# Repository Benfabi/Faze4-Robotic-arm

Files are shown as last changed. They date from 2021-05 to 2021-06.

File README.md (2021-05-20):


# Faze4-Robotic-arm

 

Faze4 is small fully 3d printable Open source 6 axis robotic arm. It is functionally and esthetically similar to robotic arms in industry but is aimed for research, education and  anyone interested in making his own robot arm. 

The whole arm has around 1000 parts (including screws and bearings) and weights around 15 kg.

## Why this fork?

The original repository contains many links, PDFs and most likely everyhting you need to create the Faze4 robot. However, it does not really give a sense of a structured approach building it, writing software for the robot or using it in the end.

At this point, this fork is supposed to contribute. It should give a clear direction where to start and how to build it, independent of your background.

# Structure of this repo

- [0-Construction](./0-Construction): this folder contains a step by tutorial building the robot.
- [STL](./STL): this folder contains the STL files to print. The construction tutorial will let you know when each print is needed. 
- [Original](./Original): this folder contains the files from the original repository.

# Where to start ? 

It is recommended to start with the [Construction](./0-Construction) folder.

# Check the arm in action
Check the arm in action ! (https://www.youtube.com/watch?v=OHw6_l_8Tnk)

# Further Links:

- [Building instructions](./Original/Assembly%20instructions%203.1.pdf)
- [DOCS](https://faze4-robotic-arm-docs.readthedocs.io/en/latest/) Contains ALL info about the arm.
- [URDF files](https://github.com/PCrnjak/Faze4-Robotic-arm/tree/master/URDF_FAZE4)
- [Hackaday](https://hackaday.io/project/167247-faze4-robotic-arm)
- [DOCS](https://faze4-robotic-arm-docs.readthedocs.io/en/latest/)

# Project is under MIT Licence

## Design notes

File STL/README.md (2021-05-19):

# STL files

This folder contains the STL files that are needed to build the robot. 
I also put the GCode files here that I used to print the specific parts.

The printer I use is a [Original Prusa i3 MK3S+ Drucker
](https://shop.prusa3d.com/3d-drucker/181-original-prusa-i3-mk3s-drucker.html).

The slicer settings used are in the corresponding 3mf file.

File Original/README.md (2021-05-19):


# Faze4-Robotic-arm

 

Faze4 is small fully 3d printable Open source 6 axis robotic arm. It is functionally and esthetically similar to robotic arms in industry but is aimed for research, education and 
anyone interested in making his own robot arm. 
Main "selling points" of this arm that separate it from other DIY arms are:

* It is cheap <1000 dollars.
* Uses 3d printed cycloidal gearboxes which have low backlash and can be repaired really easy.
* All wires are hidden giving it really clean design.

Whole arm has around 1000 parts (including screws and bearings) and weights around 15 kg.

# Check the arm in action !
Check the arm in action ! (https://www.youtube.com/watch?v=OHw6_l_8Tnk)

# Where to start ? 

To build this robotic arm follow [Building instructions](https://github.com/PCrnjak/Faze4-Robotic-arm/blob/master/Assembly%20instructions%203.0.pdf). All general info about robotic arm is in [DOCS](https://faze4-robotic-arm-docs.readthedocs.io/en/latest/). Building instructions and DOCS go hand in hand and you need to follow both to build this arm. Building instructions are about general mechanical assembly while DOCS contain ALL info ( Electrical wiring, Low level setup, High level ROS and Matlab, tips ...).

# Contents:

- [Low level code]() coming soon
- [High level code (ROS and Matlab)]() coming soon
- [Building instructions](https://github.com/PCrnjak/Faze4-Robotic-arm/blob/master/Assembly%20instructions%203.0.pdf)
- [BOM](https://github.com/PCrnjak/Faze4-Robotic-arm/blob/master/Bom_1.2_joint2_update.xlsx) 
- [DOCS](https://faze4-robotic-arm-docs.readthedocs.io/en/latest/) Contains ALL info about the arm.
- [URDF files](https://github.com/PCrnjak/Faze4-Robotic-arm/tree/master/URDF_FAZE4) 

# Where to see more Faze4 robotic arm?
- [Youtube](https://www.youtube.com/channel/UCp3sDRwVkbm7b2M-2qwf5aQ)
- [Hackaday](https://hackaday.io/project/167247-faze4-robotic-arm)
- [DOCS](https://faze4-robotic-arm-docs.readthedocs.io/en/latest/)

# Support the project

This project is completely Open source and free to all and I would like to keep it that way, so any help 
in terms of donations or advice is really appreciated. Thank you!

Check the arm in action ! (https://paypal.me/PCrnjak?locale.x=en_US)

# Project is under MIT Licence

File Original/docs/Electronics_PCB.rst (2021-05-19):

Electronics, PCB and wiring
===========================

.. meta::
   :description lang=en: info about Electronics and PCB.
   
All electronics can also be bought from ebay and similar sites. I used cheap stepper drivers from ebay but you can buy any stepper driver that can supply enough current for the steppers.

Check how i wired my arm in this file: FAZE4 Robotic arm electronics setup.pdf on github page:
https://github.com/PCrnjak/Faze4-Robotic-arm

.. Tip::

   From experience i found out that cheaper stepper drivers tend to make more noise, so if you want quiet robot arm buy more expensive drivers. I found ones from stepperonline good.

PCB V1
------------
This PCB is first version and has some errors that will be fixed in revision 2.
Board was created in Altium Circuitmaker and all files can be found here:

.. Warning::

  I recommend waiting for next version since this one has alot of errors.

* `All files for PCB`_

.. _All files for PCB: https://github.com/PCrnjak/Faze4-Robotic-arm/blob/master/Distribution_PCB.zip

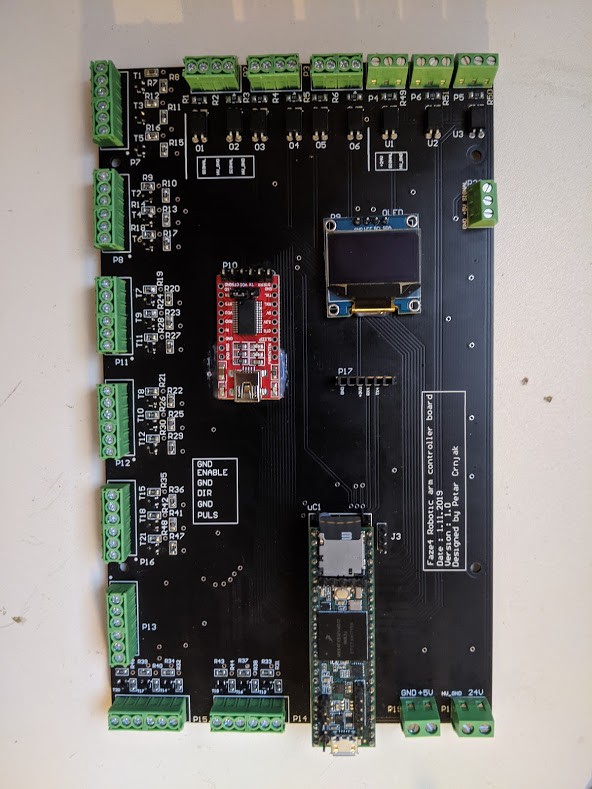
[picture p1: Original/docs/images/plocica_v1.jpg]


Upper section of PCB are Inputs for limit switches and inductive sensors. All inputs on top are isolated with optocouplers. I did that since all wires of the arm are going thru same spot, that means "high voltage" stepper wires were near low voltage limit switch wires. That caused problems where steppers induced enough voltage on limit switch wires to trigger interrupts on teensy. That is why limit switches and sensors are connected to 24v.

left side is for stepper outputs. There are also 2 stepper outputs on bottom right side.

Bottom right side has 5V input and 24V input. You need both for arm to work. In the middle we have few extra serial ports and OLED display.

When wiring stepper drivers to the PCB i used TB6600  driver pinout as reference.I planned for all drivers to be connected like picture below. HIGH signal on ENABLE + pin would enable stepper drivers. Now i made some mistakes and not all drivers can be connected like that.

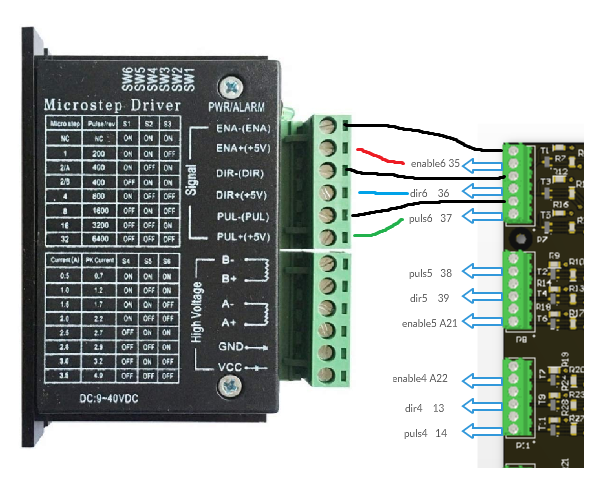
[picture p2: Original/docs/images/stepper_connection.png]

    
Now i made some mistakes and not all drivers can be connected like that. In picture below you can see how to connect all drivers. As you can see for joint 5 (connector below top one) i switched enable and puls pins. That means that puls5 pin ( pin 38 on teensy) is connected to puls pin on stepper driver. I also skipped Port that has no 5V level shifter since it didnt work well.

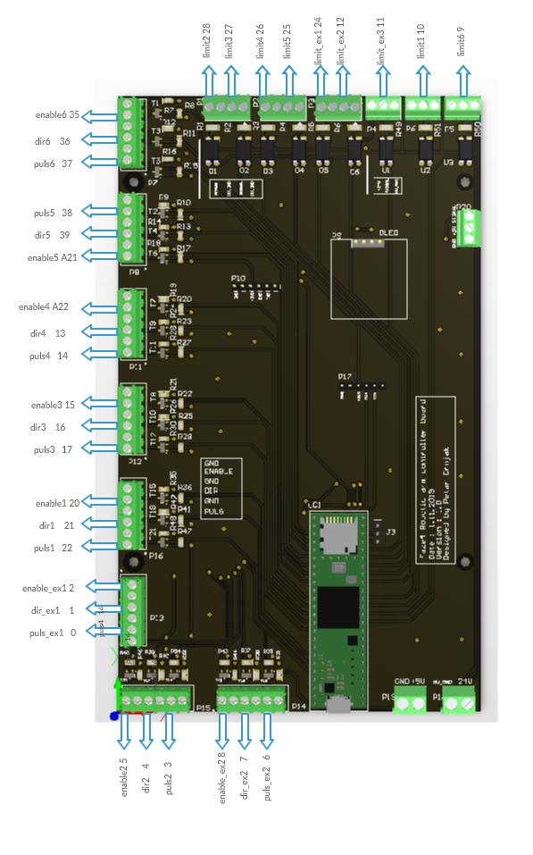
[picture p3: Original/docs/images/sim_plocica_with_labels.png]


After wiring all dir,puls and enable pins you are left with power pins on stepper driver and A- A+ B- B+ Pins. Those are quite straightforward. 
Pins that have ext in name are extra pins that are now used in my version of arm.

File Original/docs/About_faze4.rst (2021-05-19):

About Faze4
===========================

.. meta::
   :description lang=en: General info about Faze4 robotic arm.

General info
------------

Faze4 robotic arm came to be when i made a working 3d printable cycloidal gearbox and saw some potential in it. After that i designed whole arm around it. It uses 6 stepper motors, so it is a 6 axis robot arm. While designing this arm i focused on low backlash and good design of arm. All wires are hidden and arm is really rigid even tho it is 3d printed. Total cost of the arm is around 1000 - 1500 dollars.

.. note::

    This project is still work in progress. Part that is work in progress is control cabinet, that means that the arm can be built and it     will work without the cabinet.
    
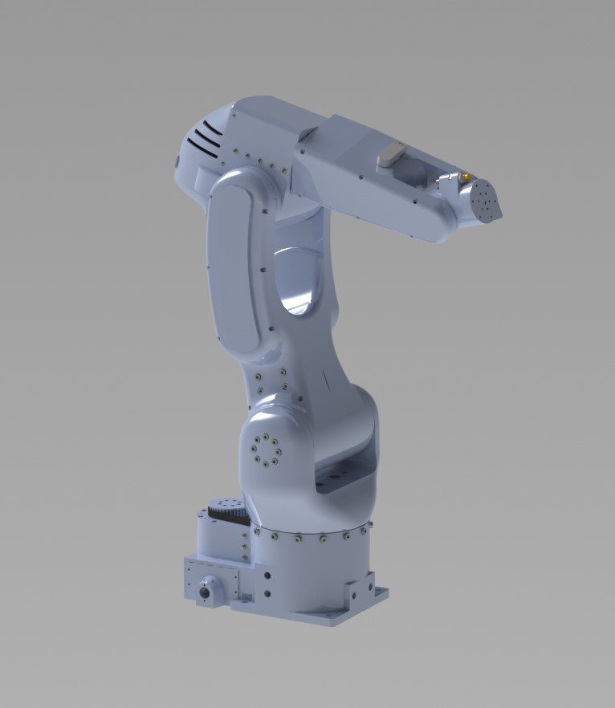
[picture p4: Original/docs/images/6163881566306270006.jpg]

    
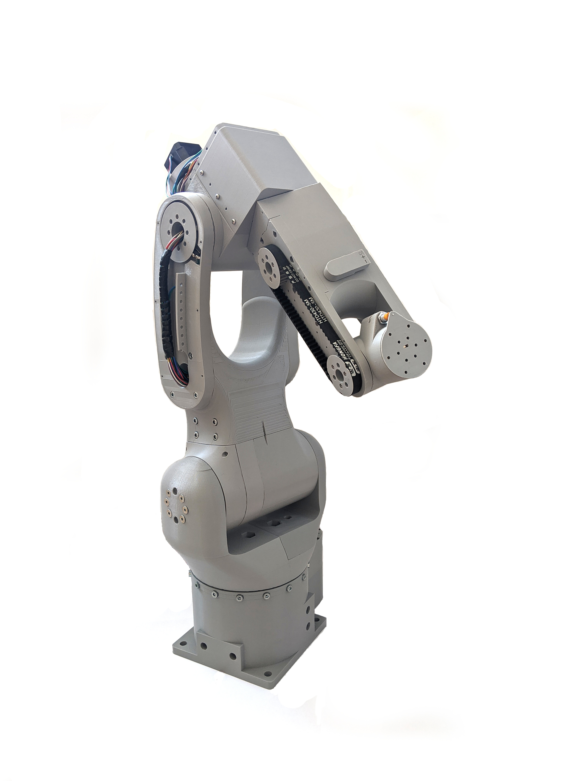
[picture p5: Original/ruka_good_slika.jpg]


Esthetic design was inspired by FANUC’s LR Mate 200iD. 
Goal was also to hide all wires in the arm like most industrial arms do. 
Only visible wires (or pipes) would be ones for gripper. 

Weight of the arm is around 14-15 kg , but it can be reduced by printing with less infill.

Low level control for the arm runs on teesny 3.5, while high level (inverse kinematics, simulations) are only on Matlab code atm, but I am working on ROS implementation and porting my Matlab code to Python.

Table of contents
-----------------

On this read the docs page you will find:

* How is arm desinged and desing decisions
* Printing tips
* Electronics guide and PCB
* Building instructions for the arm
* All code and programs used
* How to test and troubleshoot
* Sources 
* Where to buy parts

Check the arm in action !
-------------------------

.. raw:: html

    <div style="text-align: center; margin-bottom: 2em;">
    <iframe width="100%" height="350" src="https://www.youtube.com/embed/-qTVx23o6C0?rel=0" frameborder="0" allow="autoplay; encrypted-media" allowfullscreen></iframe>
    </div>

Support the project
-------------------

This project is completely Open source and free to all and I would like to keep it that way, so any help 
in terms of donations or advice is really appreciated. Thank you!

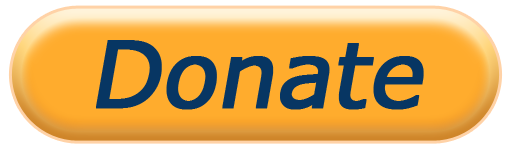
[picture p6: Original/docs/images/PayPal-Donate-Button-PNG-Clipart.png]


Thanks to the:
--------------
* `Peter Corke for his amazing robotics toolbox for Matlab`_
* `Maximilian_Schommer for his cycloidal drive generator`_

.. _Peter Corke for his amazing robotics toolbox for Matlab: https://petercorke.com/toolboxes/robotics-toolbox/
.. _Maximilian_Schommer for his cycloidal drive generator: https://forum.onshape.com/discussion/7567/cycloidal-gear-generator

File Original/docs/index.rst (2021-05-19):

.. Read the Docs documentation master file, made by Petar Crnjak.

Faze4 Robotic arm documentation
==================================================

Contents:

.. toctree::
   :maxdepth: 2
   :glob:

   *

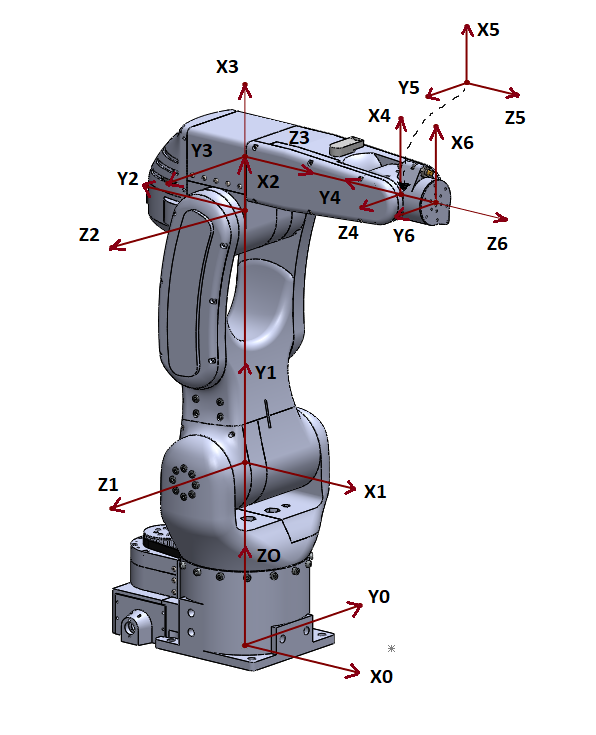
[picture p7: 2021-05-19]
Original/docs/images/OSI_v2.png

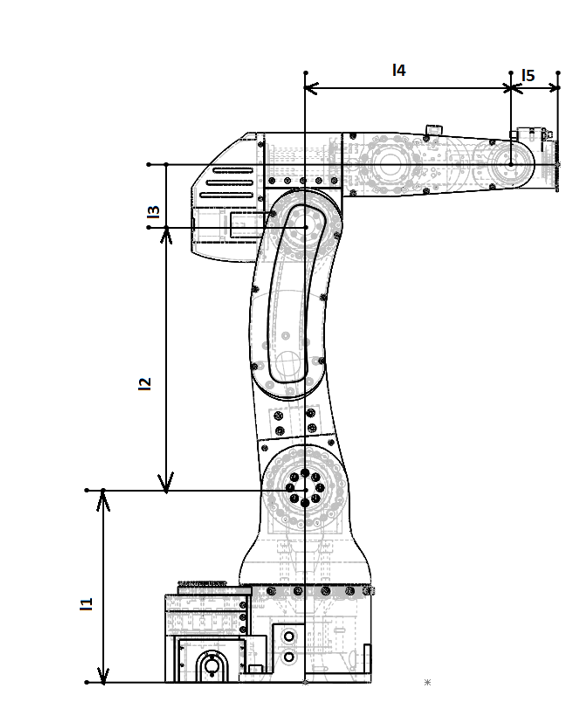
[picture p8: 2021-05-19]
Original/docs/images/robot_dim.png

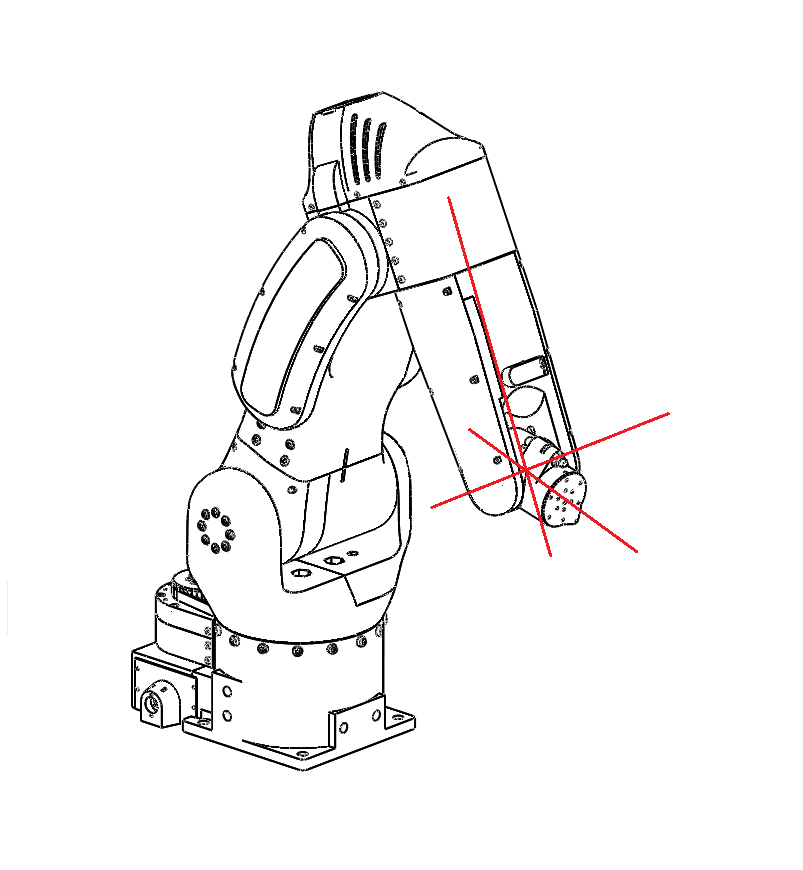
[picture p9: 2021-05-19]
Original/docs/images/slikaosirotacije.png

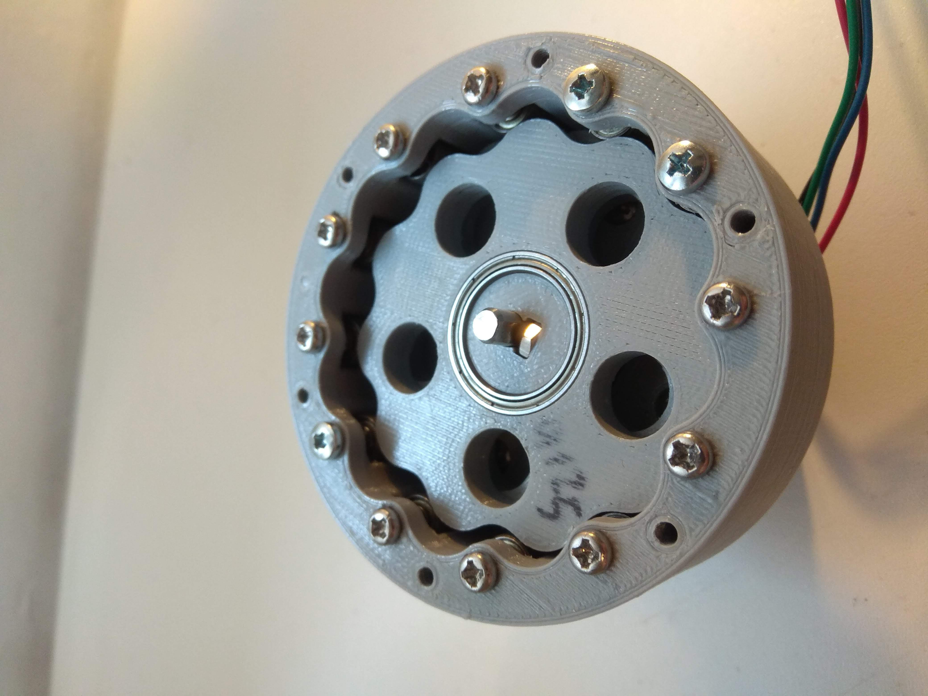
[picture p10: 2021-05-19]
Original/docs/images/reducer.jpg

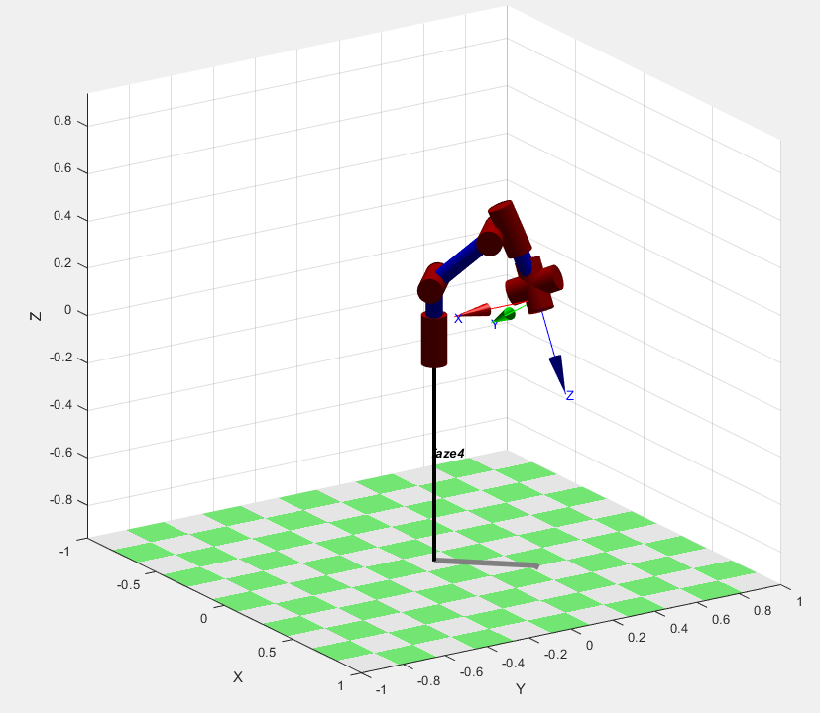
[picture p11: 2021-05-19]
Original/docs/images/30&180&90.png

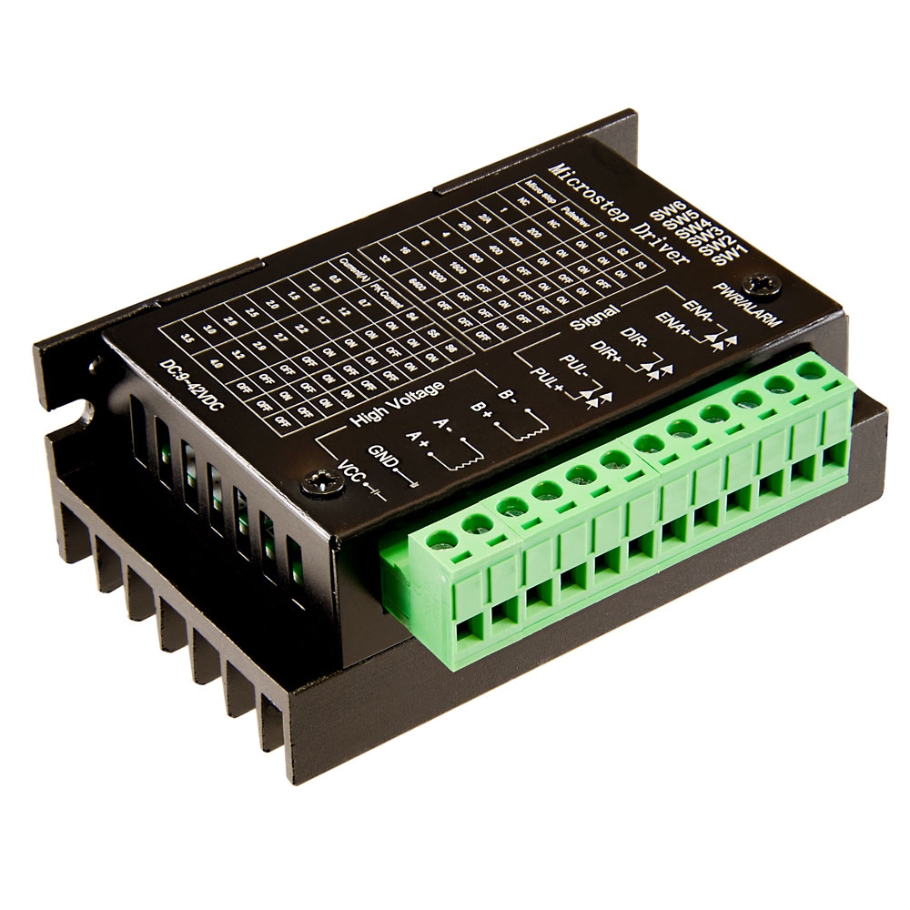
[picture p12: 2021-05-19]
Original/docs/images/tb6600.jpg

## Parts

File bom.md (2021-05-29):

# Bill of Materials

## Screws

| Diameter, length | Type | Quantity |
| ---- | --- | --- |
| M2 5mm screw | philips pan head | 3 |
| M2 8 mm screw | philips pan head | 8 |
| M2 10-12 mm screw | philips pan head | 7 |
| M3 4mm set screw | Hex | 6 |
| M3 5mm screws | philips pan head | 12 |
| M3 10 mm screw | philips pan head | 54 |
| M3 15mm screw | philips pan head | 54 |
| M3 20mm screw | philips pan head | 53 |
| M3 25mm screws | philips pan head | 64 |
| M3 30 mm screw | philips pan head | 52 |
| M5 8 mm screw | Hex socket cap | 12 |
| M5 20 mm screw | Hex socket cap | 27 |
| M5 25 mm screw | Hex socket cap | 8 |
| M5 30 mm screw | Hex socket cap | 13 |
| M5 40 mm screw | Hex socket cap | 10 |
| M10 60 mm screw | Hex socket cap | 4 |

## Nuts

| Type | Quantity |
| --- | --- |
| M2 nuts | 2 |
| M3 nuts | 6 |
| M5 nuts |	15 |
| M8 nuts (included with sensor, see other stuff) | 4 |
| M10 nuts | 4 |
| M12 nuts | 4 |

## Ball Bearings

| Ball Bearing Type | Quantity |
| --- | --- |
|  35x47x7  | 8 |
|  3x8x4 | 200 |
|  17x23x4  | 4 |
|  15x28x7  | 6 |
|  3x10x4 | 40 |
|  50x67x7  | 8 |
|  5x10x4 | 32 |
|  5x16x5 | 13 |
|  20x27x4  | 2 |

## Motors

| Nema Type | Quantity |
| --- | --- |
| Nema 14 L=33mm w/19:1 gearbox	| 1 |
| Nema 17 Bipolar  12V 42x42x40mm |	2 |
| Nema 23 Bipolar 0.9deg 2.8A 2.5V 57x57x56mm |	1 |
| Nema 23 Bipolar 4A 2.26V 57x57x84mm	| 1 |
| Nema 23 Bipolar 1.5A 5.4V 57x57x56mm | 1 |

## Other stuff

| Type | Quantity |
| ---- | --- |
| HTD 5M 430 mm timing belt 10 mm wide | 1 |
| HTD 5M 490 mm timing belt 10 mm wide | 1 |
| HTD 5M 285 mm timing belt 10mm wide | 1 |
| Inductive Sensor (Heschen M8 Inductive Proximity Sensor Switch Non-Shield Type LJ8A3-2-Z/BX Detector 2 mm 10-30VDC 200mA NPN Normally Open (NO) 3-Wire -> Includes 2xM8 nuts) | 2 |
| M3 4mm brass inserts | 12 |
| Micro limit switch | 3 |
| Roller limit switches | 2 |

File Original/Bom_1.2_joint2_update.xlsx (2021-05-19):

Parts marked with this colour are updated,they are no same as in previous versions of BOM and building instructions
Screws: |  |  | 3D Printed parts:
diameter , lenght | Type | quantity | Name | quantity
M2 5mm screw | philips pan head | 3 | Joint 6 Output shaft | 1
M3 5mm screw | philips pan head | 12 | Wrist case | 1
M3 4mm set screw | Hex | 6 | Wrist cover | 1
M3 25mm screw | philips pan head | 64 | Forearm main case | 1
M2 8 mm screw | philips pan head | 8 | J5 ring rollers | 12
M3 20mm screw | philips pan head | 53 | 11:1 cyclo disc | 4
M3 10 mm screw | philips pan head | 54 | Eccentric shaft J5 | 1
M3 15mm screw | philips pan head | 54 | Servo gripper plug | 1
M5 30 mm screw | Hex socket cap | 13 | joint 5 output shaft | 1
M5 20 mm screw | Hex socket cap | 27 | joint 5 output spacers | 10
M5 8 mm screw | Hex socket cap | 12 | joint 5 switch trigger | 1
M3 30 mm screw | philips pan head | 52 | Forearm top cover | 1
M5 25 mm screw | Hex socket cap | 8 | J5 28 teeth pulley | 2
M2 10-12 mm screw | philips pan head | 7 | Joint 4 output shaft | 1
M5 40 mm screw | Hex socket cap | 10 | Joint 4 motor case | 1
M10 60 mm screw | Hex socket cap | 4 | J4 ring spacers | 12
 |  |  | Eccentric shaft J4 | 1
 |  |  | J4 cyclo output shaft | 1
 |  |  | joint 4 output spacers | 10
Bearings: |  |  | Joint 4 top cover | 1
Type | quantity |  | Joint 3 main case | 1
Ball bearing 35x47x7 | 8 |  | Joint 3 cover | 1
Ball bearing 3x8x4 | 200 |  | 15:1 cyclo disc | 4
Ball bearing 17x23x4 | 4 |  | Joint 3 ring spacers | 32
Ball baering 15x28x7 | 6 |  | Joint 3 eccentric shaft | 1
Ball bearing 3x10x4 | 40 |  | Joint 3 output shaft | 1
Ball bearing 50x67x7 | 8 |  | Joint 3 top cover | 1
Ball bearing 5x10x4 | 32 |  | Joint 4 offset | 1
Ball bearing 5x16x5 | 13 |  | Joint 4 limit switch cover | 1
Ball bearing 20x27x4 | 2 |  | Joint 4 pulley 28 teeth | 1
 |  |  | 26 teeth Joint 4 pulley | 1
Other: |  |  | Fork | 1
Name | quantity |  | Fork_motor | 1
M3 4mm brass inserts | 12 |  | Fork_wires | 1
M2 nuts | 2 |  | Joint 3 limit trigger | 1
M3 nuts | 6 |  | Joint 2 main case | 1
Inductive sensor | 2 |  | Joint 2 cover | 1
M8 nuts (usually included with sensor | 4 |  | Joint 2 eccentric shaft | 1
Nema 14 L=33mm w/19:1 gearbox | 1 |  | Joint 2 cyclo disc | 2
Nema 17 Bipolar 12V 42x42x40mm | 2 |  | Joint 2 ring spacer | 28
Pneumatic bulkhead connector 4mm xM12 thread | 2 |  | Joint 2 output shaft | 1
M12 nuts | 4 |  | Joint 2 top cover | 1
4mm pneumatic tube | 1 |  | Rotating base wires | 1
Micro limit switch | 3 |  | Rotating base motor | 1
HTD 5M 430 mm timing belt 10 mm wide | 1 |  | Joint 1 output shaft | 1
Nema 23 Bipolar 0.9deg 2.8A 2.5V 57x57x56mm | 1 |  | Joint 1 main case | 1
J4 beltv = HTD belt 5M 285 10mm wide | 1 |  | Joint 1 cover | 1
Nema 23 Bipolar 4A 2.26V 57x57x84mm | 1 |  | Joint 1 ring spacers | 32
M5 nuts | 15 |  | Joint 1 eccentric shaft | 1
M10 nuts | 4 |  | Joint 1 cyclo output shaft | 1
Roller limit switches | 2 |  | Joint 1 top cover | 1
Nema 23 Bipolar 1.5A 5.4V 57x57x56mm | 1 |  | Main base | 1
HTD 5M 490 mm timing belt 10 mm wide | 1 |  | 36 teeth pulley | 1
 |  |  | Ball bearing retainer | 1
 |  |  | Shaft blocker | 1
 |  |  | Forearm motor lid | 1
Total not 3d printed parts : | 764 |  | Forearm wires lid | 1
 |  |  | Elbow lid | 1
Total 3d printed parts : | 197 |  | Upper arm lid | 1
 |  |  | Rotating base lid | 1
Total parts | 961

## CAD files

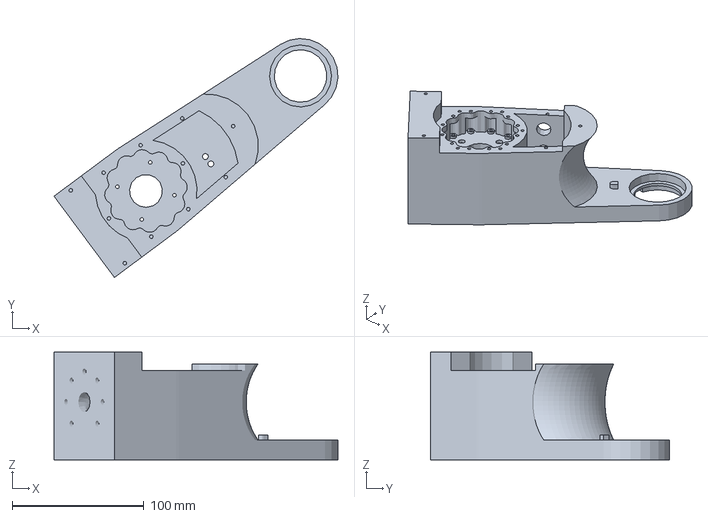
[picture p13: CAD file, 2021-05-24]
STL/b_Forearm/Forearm main case.3mf
216.0 x 181.7 x 82.0 mm

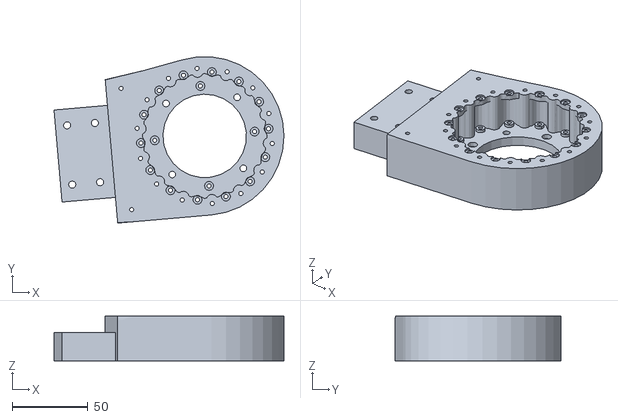
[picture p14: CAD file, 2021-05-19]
STL/Arm+J2/J2 cyclo/Joint 2 main case.STL
152.2 x 110.0 x 29.6

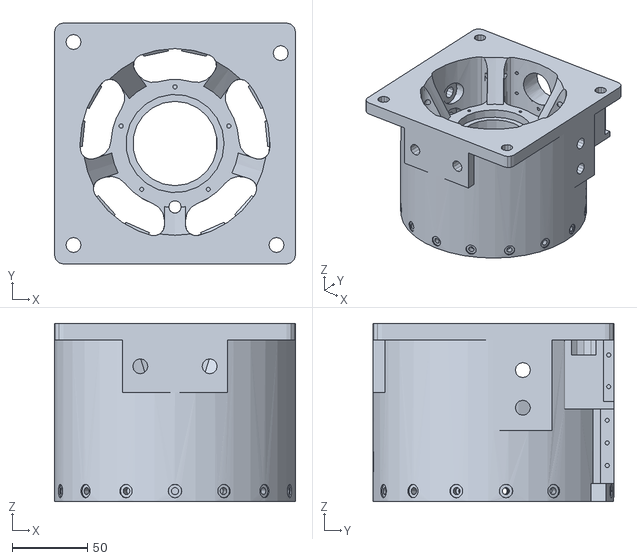
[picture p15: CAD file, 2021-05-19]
STL/Base/Main base.STL
160.0 x 160.0 x 118.3

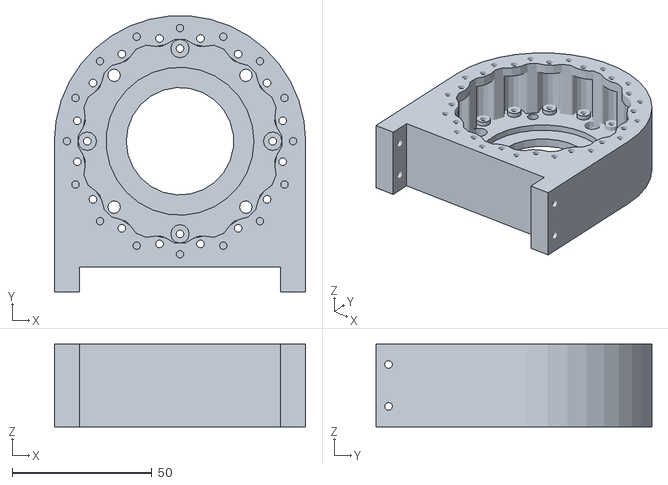
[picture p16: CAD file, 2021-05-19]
STL/Base/Joint 1 main case.STL
90.0 x 98.8 x 29.6

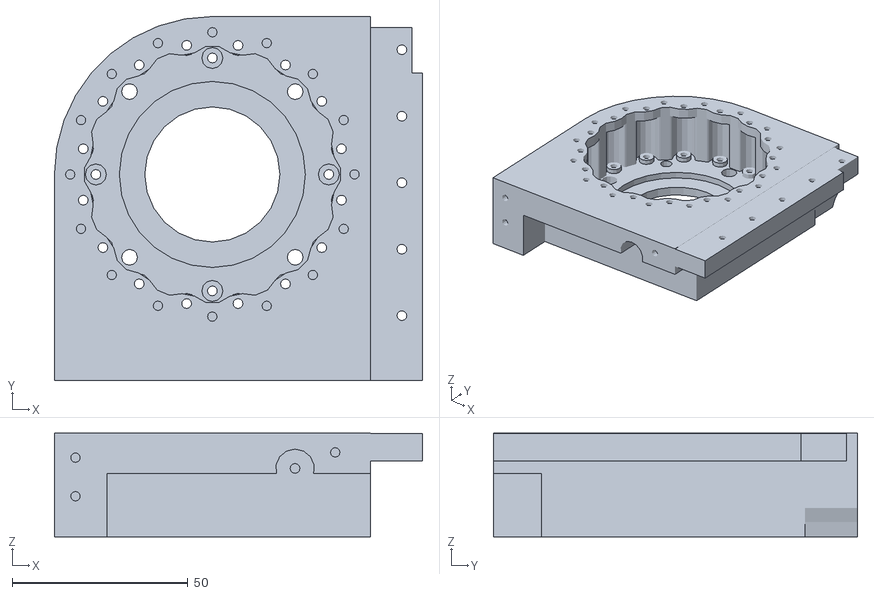
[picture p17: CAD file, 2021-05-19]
STL/c_Elbow/Joint 3 main case.STL
104.9 x 103.7 x 29.6

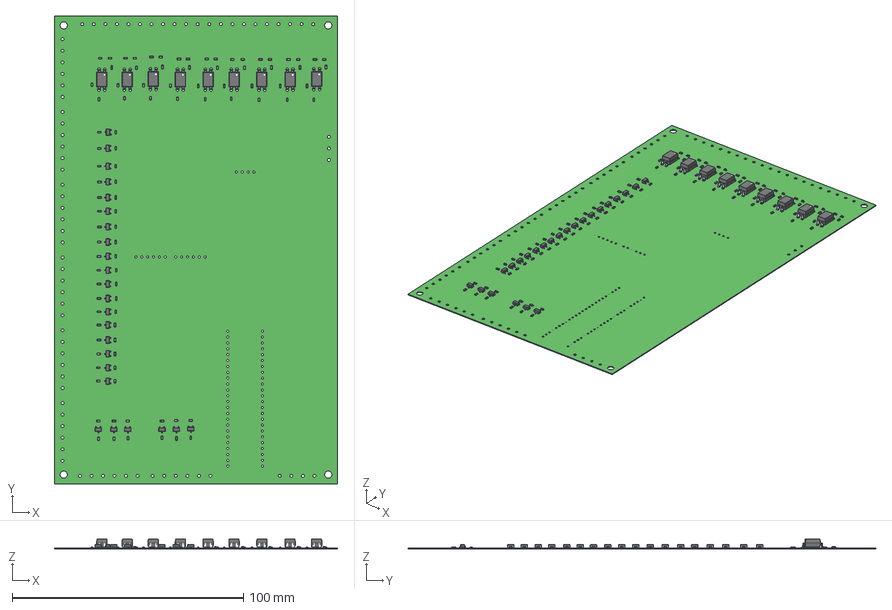
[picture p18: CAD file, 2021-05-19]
Original/Faze4_DIST_board_v2_files/Faze4_dist_v2_STEP.step
122.5 x 202.5 x 4.26 mm
Board
0603_resistor x 84
LTV-817S x 9
LED_0603_Base_YELLOW x 9
LED_0603_Lens_YELLOW x 9
sot-23-3 x 24

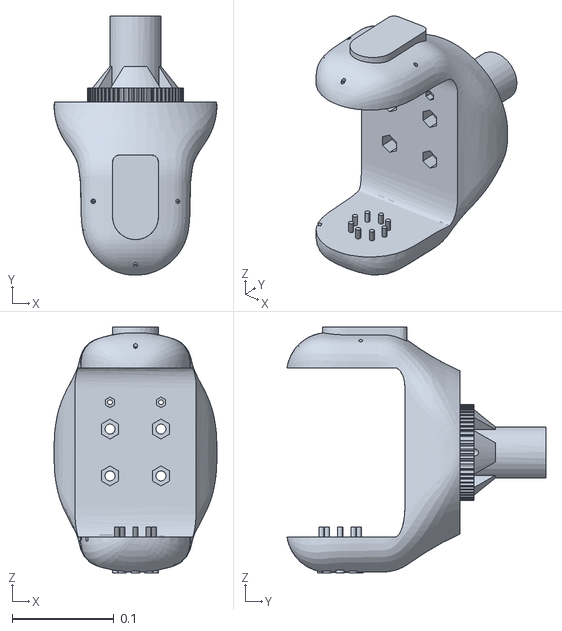
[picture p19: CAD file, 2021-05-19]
Original/URDF_FAZE4/meshes/rotary_base.STL
0.16 x 0.254 x 0.241

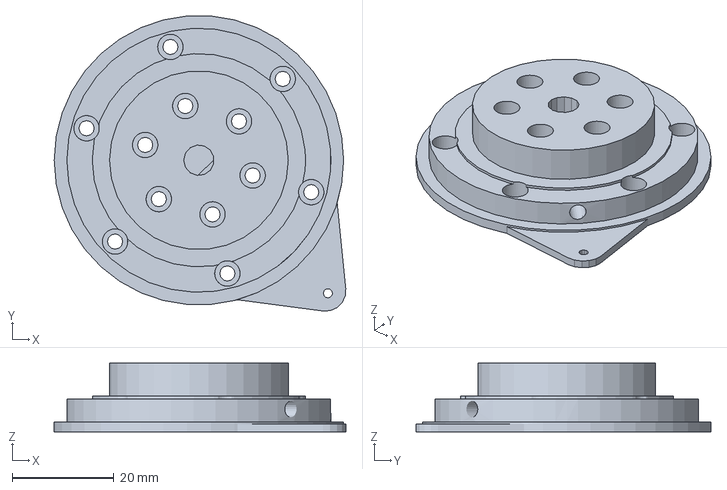
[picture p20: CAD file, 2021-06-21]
STL/a_Wrist/Joint-6-output-shaft.3mf
57.4 x 58.1 x 13.5 mm

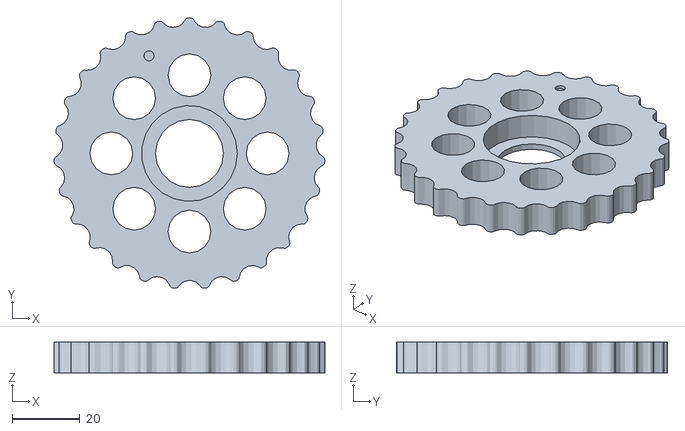
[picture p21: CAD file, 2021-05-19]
STL/Arm+J2/J2 cyclo/Joint 2 cyclo disc.STL
79.8 x 79.6 x 9.00

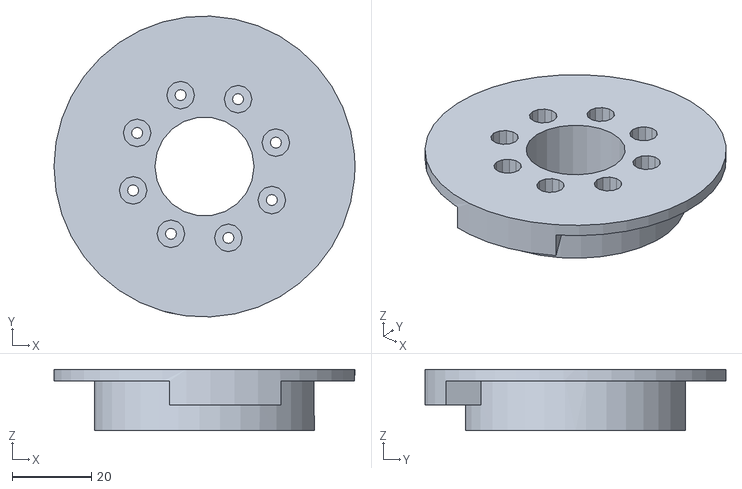
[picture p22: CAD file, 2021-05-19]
STL/Arm+J2/joint2_limit_trigger.STL
76.0 x 75.9 x 15.5

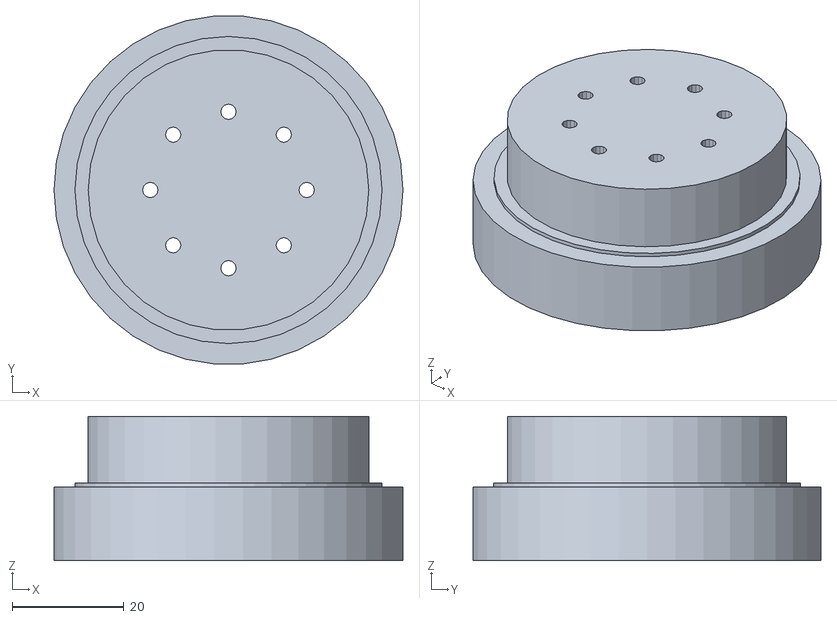
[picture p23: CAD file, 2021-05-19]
STL/Base/joint 1 cyclo output shaft.STL
62.5 x 62.3 x 25.8

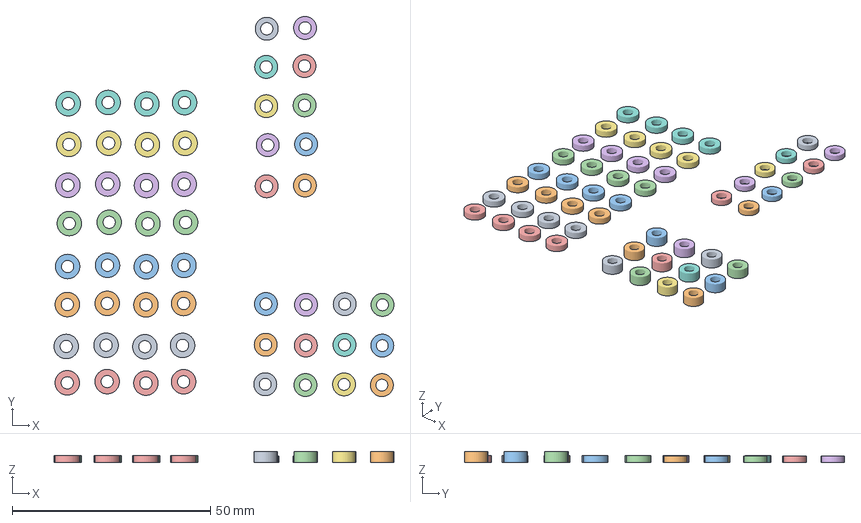
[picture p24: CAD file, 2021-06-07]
STL/c_Elbow/spacers.3mf
85.8 x 96.0 x 2.80 mm
Joint 3 ring spacers.STL x 4
Joint 4 ring spacers.STL x 12
Joint 4 Output spacers.STL x 10

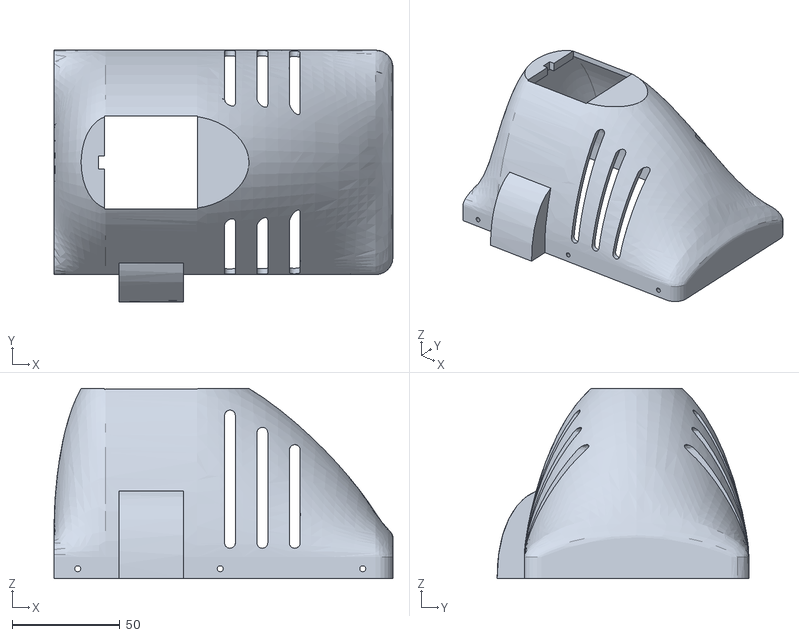
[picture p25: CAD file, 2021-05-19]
STL/Cosmetic/Elbow lid.STL
157.0 x 116.6 x 88.0

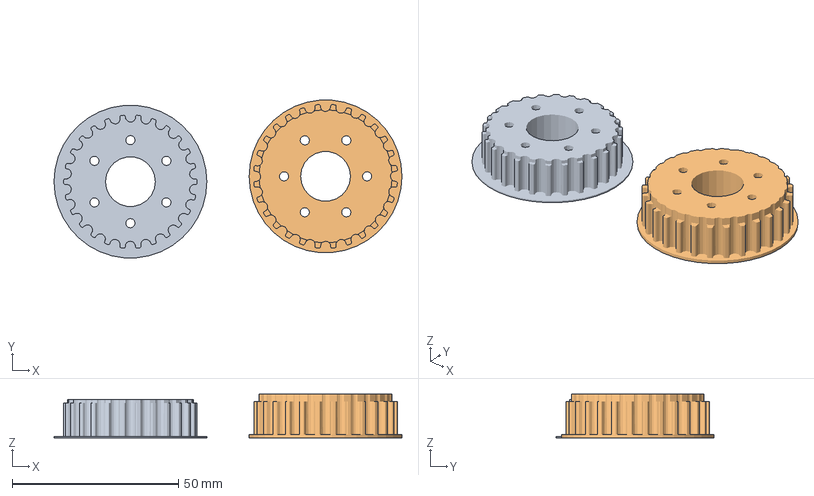
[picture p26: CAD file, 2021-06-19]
STL/d_LowerArmAssembly/Joint 4 pulley.3mf
104.7 x 47.4 x 13.2 mm
Joint 4 pulley 26 teeth.STL
Joint 4 pulley 28 teeth.STL

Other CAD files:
STL/e_ArmAssembly/Fork motor.STL
STL/Rework_parts/27to1 disc _ rework.STL
STL/Rotating base/Joint 1 output shaft.STL
STL/wire_harness.STL
Original/URDF_FAZE4/meshes/hvataljka.STL
Original/URDF_FAZE4/meshes/lakat.STL
Original/URDF_FAZE4/meshes/nadlaktica.STL
Original/URDF_FAZE4/meshes/podlaktica.STL
Original/URDF_FAZE4/meshes/saka.STL
STL/Arm+J2/J2 cyclo/Joint 2 cover.STL
STL/Arm+J2/J2 cyclo/Joint 2 eccentric shaft.STL
STL/Arm+J2/J2 cyclo/Joint 2 output shaft.STL
STL/Arm+J2/J2 cyclo/Joint 2 ring spacers.STL
STL/Arm+J2/J2 cyclo/Joint 2 top case.STL
STL/Base/15_1 cyclo disc.STL
STL/Base/36 teeth pulley.STL
STL/Base/Ball bearing retainer.STL
STL/Base/Joint 1 cover.STL
STL/Base/Joint 1 eccentric shaft.STL
STL/Base/Joint 1 ring spacers.STL
STL/Base/Joint1 top cover.STL
STL/Base/Shaft blocker.STL
STL/Base/Wire harness.STL
STL/Cosmetic/Forearm motor lid.STL
STL/Cosmetic/Forearm wires lid.STL
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

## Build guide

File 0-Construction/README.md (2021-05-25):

# Construction

The construction of the Faze4 is structured in different stages.
At every stage, there is a list of tests provided that can be done in order to ensure correct functionality.

Every build stage consists of:
- Name and Tutorial.
- Bill of Materials (BoM) for the stage.
- List of 3D prints needed to complete the stage.
- Test cases ensuring correct assembly.

There are the following build stages (*work in progress*):
| Name | BoM | 3D Prints | Tests |
| ---- | --- | --- | ----- |
| [Wrist](./a_Wrist.md) | [BoM](./a_Wrist.md#bill-of-material)  | [15h25m of printing](./a_Wrist.md#3d-prints) | [X Test Cases](./a_Wrist.md#testing)  |
| [Forearm](./b_Forearm.md) | [BoM](./b_Forearm.md#bill-of-material)  | [2d3h30m of printing](./b_Forearm.md#3d-prints) | [X Test Cases](./b_Forearm.md.md#testing)  |

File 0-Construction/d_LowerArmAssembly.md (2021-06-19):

# Forearm

Before you start, make sure you got the material and 3D prints below ready.

## Bill of Material

| Part | Quantity |
| ---- | --- |
| M3 15 mm set screw | 12 |
| M3 20mm-25mm screws | 6 |
| Joint 4 belt | 1 |

## 3D prints

With the given GCode, there is a total of 2d 3h 30m of printing choosing the combined print.

| STL File | Quantity | 3mf File | gcode |
| --- | --- | --- | ----- |
| Joint 4 pulley 28 teeth | 1 | - | - |
| Joint 4 pulley 26 teeth | 1 | - | - |

For the ones who think that are too many prints, we combined the fast prints and get a total of 3 prints and a total print time of 2d 3h 30m.

| Combined file | 3mf File | gcode |
| --- | --- | ----- |
| Joint 4 Pulleys | [3mf](../STL/d_LowerArmAssembly/joint%204%20pulley.3mf) | [gcode PLA 1d11h42m](../STL/d_LowerArmAssembly/Joint%204%20pulley_0.2mm_PLA_MK3S_2h41m.zip) |

## Construction

Steps 31-36
[Building instructions](../Original/Assembly%20instructions%203.1.pdf)
- TODO

## Testing

- TODO

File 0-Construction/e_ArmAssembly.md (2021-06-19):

# Forearm

Before you start, make sure you got the material and 3D prints below ready.

## Bill of Material

| Part | Quantity |
| ---- | --- |
| M2 8mm screws | 2 |
| M3 20 mm screws | 8 |
| M3 30 mm screw | 8 |
| M5 HEX 20 mm screw | 7 |
| M5 HEX 30 mm screw | 5 |
| Ball bearing 35x47x7 | 1 |
| Micro limit switch | 1 |

## 3D prints

With the given GCode, there is a total of 2d 3h 30m of printing choosing the combined print.

| STL File | Quantity | 3mf File | gcode |
| --- | --- | --- | ----- |
| Fork | 1 | - | - |
| Fork Motor | 1 | - | - |
| Fork wires | 1 | - | - |
| Joint 3 limit trigger | 1 | - | - |

For the ones who think that are too many prints, we combined the fast prints and get a total of 3 prints and a total print time of 2d 3h 30m.

| Combined file | 3mf File | gcode |
| --- | --- | ----- |
| Joint 4 Pulleys | [3mf](../STL/d_LowerArmAssembly/joint%204%20pulley.3mf) | [gcode PLA 1d11h42m](../STL/d_LowerArmAssembly/Joint%204%20pulley_0.2mm_PLA_MK3S_2h41m.zip) |

## Construction

Steps 37-43
[Building instructions](../Original/Assembly%20instructions%203.1.pdf)
- TODO

## Testing

- TODO

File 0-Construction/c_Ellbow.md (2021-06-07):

# Forearm

Before you start, make sure you got the material and 3D prints below ready.

## Bill of Material

| Part | Quantity |
| ---- | --- |
| M2 8mm screws | 4 |
| M3 4mm set screw | 1 |
| M3 5mm screws | 4 |
| M3 10mm screws | 8 |
| M3 15mm screws | 1 |
| M3 20mm screws | 11 |
| M3 25mm screws | 28 |
| M3 30mm screws | 16 |
| M3 nut | 2 |
| M3 4mm set screw | 1 |
| M5 8mm HEX screws | 4 |
| Ball bearing 3x8x4 | 82 |
| Ball bearing 3x10x4 | 32 |
| Ball bearing 15x28x7 | 2 |
| Ball bearing 17x23x4 | 2 |
| Ball bearing 35x47x7 | 3 |
| Ball bearing 50x65x7 | 2 |
| Nema 17 stepper | 1 |
| Nema 23 Bipolar 0.9deg 2.8A 2.5V 57x57x56mm | 1 |
| Micro Limit switch | 1 |

## 3D prints

With the given GCode, there is a total of 2d 3h 30m of printing choosing the combined print.

| STL File | Quantity | 3mf File | gcode |
| --- | --- | --- | ----- |
| 11:1 cyclo disc | 2 | - | - |
| 15:1 cyclo disc | 2 | - | - |
| Joint 4 cycle output shaft | 1 | - | - |
| Joint 4 eccentric shaft | 1 | - | - |
| Joint 4 limit switch cover | 1 | - | - |
| Joint 4 motor case | 1 | - | - |
| Joint 4 Offset | 1 | - | - |
| Joint 4 output spacers | 10 | - | - |
| Joint 4 ring spacers | 12 | - | - |
| Joint 4 top cover | 1 | - | - |
| Join 3 cover | 1 | - | - |
| Joint 3 eccentric shaft | 1 | - | - |
| Joint 3 main case | 1 | - | - |
| Joint 3 output shaft | 1 | - | - |
| Joint 3 ring spacers | 32 | - | - |
| Joint 3 top cover | 1 | - | - |

For the ones who think that are too many prints, we combined the fast prints and get a total of 3 prints and a total print time of 2d 3h 30m.

| Combined file | 3mf File | gcode |
| --- | --- | ----- |
| Cyclo Discs | [3mf](../STL/c_Ellbow/cyclo%20discs.3mf) | [gcode PLA 5h8m](../STL/c_Ellbow/cyclo%20discs_0.2mm_PLA_MK3S_5h8m.gcode) |
| Spacers | [3mf](../STL/c_Ellbow/spacers.3mf) | [gcode PLA 27m](../STL/c_Ellbow/spacers_0.2mm_PLA_MK3S_27m.gcode) |
| Joint 3 | [3mf](../STL/c_Ellbow/joint%203.3mf) | [gcode PLA 1d18h46m](../STL/c_Ellbow/joint%203_0.2mm_PLA_MK3S_1d18h46m.zip) |
| Joint 4 | [3mf](../STL/c_Ellbow/joint%204.3mf) | [gcode PLA 1d11h42m](../STL/c_Ellbow/joint%204_0.2mm_PLA_MK3S_1d11h42m.zip) |

## Construction

Steps 18-30
[Building instructions](../Original/Assembly%20instructions%203.1.pdf)
- TODO

## Testing

- TODO

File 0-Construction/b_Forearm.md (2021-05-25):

# Forearm

Before you start, make sure you got the material and 3D prints below ready.

## Bill of Material

| Part | Quantity |
| ---- | --- |
| M2 8mm screws | 2 |
| M3 4mm set screws | 1 |
| M3 5mm screws | 4 |
| M3 10 mm screws | 6 |
| M3 15 mm screws | 23 |
| M3 20mm screws | 5 |
| M3 25mm screws | 12 |
| M5 20mm IMBUS screw | 7 |
| M3 nut | 1 |
| Ball bearing 3x8x4 | 38 |
| Ball bearing 17x23x4 | 2 |
| Ball bearing 35x47x7 | 3 |
| HTD 5M 430 mm timing belt 10 mm wide | 1 |
| Nema 17 stepper | 2 |
| Micro limit switch | 1 |

## 3D prints

With the given GCode, there is a total of 2d 3h 30m of printing choosing the combined print.

| STL File | Quantity | 3mf File | gcode |
| --- | --- | --- | ----- |
| 11:1 cyclo disc | 2 | [3mf](../STL/b_Forearm/11_1%20cyclo%20disc.3mf) | [gcode PLA 59m](../STL/b_Forearm/11_1%20cyclo%20disc_0.2mm_PLA_MK3S_59m.gcode) |
| Forearm main case | 1 | [3mf](../STL/b_Forearm/Forearm%20main%20case.3mf) | [gcode PLA 1d6h](../STL/b_Forearm/Forearm%20main%20case_0.2mm_PLA_MK3S_1d6h0m.gcode) |
| Forearm top cover | 1 | [3mf](../STL/b_Forearm/Forearm%20top%20cover.3mf) | [gcode PLA 7h37m](../STL/b_Forearm/Forearm%20top%20cover_0.2mm_PLA_MK3S_7h37m.gcode) |
| Joint 4 shaft | 1 | [3mf](../STL/b_Forearm/Joint%204%20shaft.3mf) | [gcode PLA 6h16m](../STL/b_Forearm/Joint%204%20shaft_0.2mm_PLA_MK3S_6h16m.gcode) |
| Joint 5 28 teeth pulley | 1 | [3mf](../STL/b_Forearm/Joint%205%2028%20teeth%20pulley.3mf) | [gcode PLA 1h18m](../STL/b_Forearm/Joint%205%2028%20teeth%20pulley_0.2mm_PLA_MK3S_1h18m.gcode) |
| Joint 5 Eccentric shaft | 1 | [3mf](../STL/b_Forearm/Joint%205%20Eccentric%20shaft.3mf) | [gcode PLA 31m](../STL/b_Forearm/Joint%205%20Eccentric%20shaft_0.2mm_PLA_MK3S_31m.gcode) |
| Joint 5 Output shaft | 1 | [3mf](../STL/b_Forearm/Joint%205%20Output%20shaft.3mf) | [gcode PLA 1h56m](../STL/b_Forearm/Joint%205%20Output%20shaft_0.2mm_PLA_MK3S_1h56m.gcode) |
| Joint 5 Output spacers | 10 | [3mf](../STL/b_Forearm/Joint%205%20Output%20spacers.3mf) | [gcode PLA 4m](../STL/b_Forearm/Joint%205%20Output%20spacers_0.2mm_PLA_MK3S_4m.gcode) |
| Joint 5 Ring Rollers | 12 | [3mf](../STL/b_Forearm/Joint%205%20ring%20rollers.3mf) | [gcode PLA 8m](../STL/b_Forearm/Joint%205%20ring%20rollers_0.2mm_PLA_MK3S_8m.gcode) |
| Joint 5 switch trigger | 1 | [3mf](../STL/b_Forearm/Joint%205%20switch%20trigger.3mf) | [gcode PLA 48m](../STL/b_Forearm/Joint%205%20switch%20trigger_0.2mm_PLA_MK3S_48m.gcode) |
| Servo gripper plug | 1 | [3mf](../STL/b_Forearm/Servo_gripper_plug.3mf) | [gcode PLA 1h2m](../STL/b_Forearm/Servo_gripper_plug_0.2mm_PLA_MK3S_1h2m.gcode) |

For the ones who think that are too many prints, we combined the fast prints and get a total of 3 prints and a total print time of 2d 3h 30m.

| STL File | 3mf File | gcode |
| --- | --- | ----- |
| Forearm main case | [3mf](../STL/b_Forearm/Forearm%20main%20case.3mf) | [gcode PLA 1d6h](../STL/b_Forearm/Forearm%20main%20case_0.2mm_PLA_MK3S_1d6h0m.gcode) |
| Forearm top cover | [3mf](../STL/b_Forearm/Forearm%20top%20cover.3mf) | [gcode PLA 7h37m](../STL/b_Forearm/Forearm%20top%20cover_0.2mm_PLA_MK3S_7h37m.gcode) |
| Print Combination | [3mf](../STL/b_Forearm/Print%20Combination.3mf) | [gcode PLA 13h53m](../STL/b_Forearm/Print%20Combination_0.2mm_PLA_MK3S_13h53m.gcode) |

## Construction

Steps 5-17
[Building instructions](../Original/Assembly%20instructions%203.1.pdf)
- TODO

## Testing

- TODO

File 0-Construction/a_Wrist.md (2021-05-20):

# Wrist

Before you start, make sure you got the material and 3D prints below ready.

## Bill of Material

| Part | Quantity |
| ---- | --- |
| M2 5mm screw | 1 |
| M2 nuts | 2 |
| M2 5mm screw | 2 |
| M3 5mm screws | 4 |
| M3 4mm brass inserts | 12 |
| M3 nuts | 1 |
| M3 4mm set screw | 1 |
| M8 nuts (usually deliverd with the inductive sensor) | 2 |
| Ball bearing 35x47x7 | 1 |
| Nema 14, 19:1 gearbox motor | 1 |
| Inductive Sensor | 1 |

## 3D prints

With the given GCode, there is a total of 15h 25m of printing.

| STL File | 3mf File | gcode |
| --- | --- | ----- |
| [Joint 6 Output shaft](../STL/a_Wrist/Joint-6-output-shaft.stl) | [3mf](../STL/a_Wrist/Joint-6-output-shaft.3mf) | [gcode PLA 1h38m](../STL/a_Wrist/Joint-6-output-shaft_0.2mm_PLA_MK3S_1h38m.gcode) |
| [Wrist case](../STL/a_Wrist/Wrist-case.stl) | [3mf](../STL/a_Wrist/Wrist-case.3mf) | [gcode PLA 13h1m](../STL/a_Wrist/Wrist-case_0.2mm_PLA_MK3S_13h1m.gcode) |
| [Wrist cover](../STL/a_Wrist/Wrist-cover.stl) | [3mf](../STL/a_Wrist/Wrist-cover.3mf) | [gcode PLA 46m](../STL/a_Wrist/Wrist-cover_0.2mm_PLA_MK3S_46m.gcode) |

## Construction

Steps 1-4
[Building instructions](../Original/Assembly%20instructions%203.1.pdf)
- TODO

## Testing

- TODO

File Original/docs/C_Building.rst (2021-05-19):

Building 
===========================

.. meta::
   :description lang=en: Instructions and tips to build mechanical part of the arm.
   
.. note::

   All parts can be bought from ebay and similar online stores. I bought all steppers,drivers and PSUs from stepper online. You can buy    screws used for this arm in online stores but i sourced them locally and that was much cheaper. I also recommend to buy wires (you      will need them to extend stepper wires) locally since ones on ebay and similar stores are of questionable quality.

* `Full assembly instructions are here`_

.. _Full assembly instructions are here: https://github.com/PCrnjak/Faze4-Robotic-arm

BOM
------------
You can find bom in this excel document and in building instructions file. 

* `BOM FILE`_

.. _BOM FILE: https://github.com/PCrnjak/Faze4-Robotic-arm

.. Tip::

   I also recommend to buy more items like bearinngs and screws than you need since you might destroy or damage some in building            process.

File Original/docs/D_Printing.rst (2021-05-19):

Printing
===========================

.. meta::
   :description lang=en: Printing tips.

Filament
------------

I recommend PETG since it can withstand larger temperatures then PLA and is easier to print then ABS. Since motors can heat up i think it is best choice.

Printer
------------

All parts are designed to be printed on Prusa MK2S, so if you have printer with build volume of 250x210x200 you are good to go.

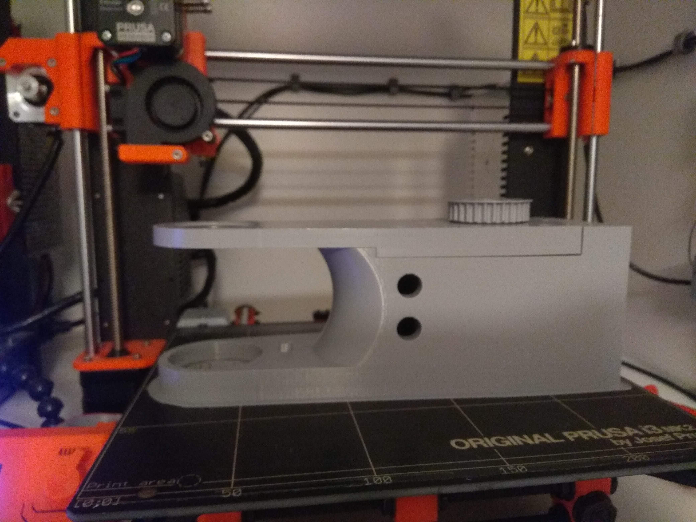
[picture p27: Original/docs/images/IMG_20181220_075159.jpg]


Print settings and tips
------------------------

I printed all smaller parts with 0.15 layer height and all larger with 0.35 layer height.For infill try to stay in 25%-30% range. I used 3 outer perimeters and 7 top and 5 bottom layers.

.. Tip::

   When printing larger parts like: x x x , try to print at slower speeds and with small accelerations.Since those parts are really        large and heavy they tend to cause missing steps when reaching the end of 3d print due the inertia.

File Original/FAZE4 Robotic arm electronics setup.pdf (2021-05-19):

FAZE4 Robotic arm electronics setup

So this is wiring guide for my setup of the arm. If you plan to build Faze4 robotic arm it might not look like this. Your wires might have different colour coding, different steppers…
So here i am going to explain some general tips.
- Microsteps for motors should be kept like ones in tables. If you change them change microstep values in software to.
- Adjust Peak current for your steppers. I used peak value of stepper drivers but actually we use RMS value of current so adjust to your RMS current!
- Voltage your stepper motor is rated
- Limit switch dir tells us what state needs to be on stepper driver DIR pin to initiate movement in DIRECTION TO HIT A LIMIT SWITCH ! This is really important! These values should be left as they are in this table. If you see your stepper is moving away from limit switch just switch any 2 wires of the same phase on stepper driver and that will change the direction. You can change it in software too but this method is easier.
- ENABLE tells us what state on enable pin of stepper drivers ENABLES the driver.
- Wires for my setup and Control pins are specific for my build of the arm.

ROBOT electronics setup

JOINT 6

Microstep | Current | Voltage | Limit switch DIR | ENABLE
400 | PK 0.7A | 24V | LOW | LOW

Wires for my setup: red,green,blue,yellow (A+,A-,B+,B-)
Control pins: GND,ENA+,GND,DIR+,PULS+

JOINT 5

Microstep | Current | Voltage | Limit switch DIR | ENABLE
400 | PK 1.2A | 24V | HIGH | ANALOG: 0

Wires for my setup: red,blue,green,black (A+,A-,B+,B-)
Control pins: GND,PULS+,GND,DIR+,ENA+

JOINT 4

Microstep | Current | Voltage | Limit switch DIR | ENABLE
400 | PK 1.2A | 24V | HIGH | ANALOG: 0

Wires for my setup: red,blue,black,green (A+,A-,B+,B-)
Control pins: GND,ENA+,GND,DIR+,PULS+

JOINT 3

Microstep | Current | Voltage | Limit switch DIR | ENABLE
400 | PK 2.2A | 24V | HIGH | LOW

Wires for my setup: red,blue,black,green (A+,A-,B+,B-)
Control pins: GND,ENA+,GND,DIR+,PULS+

JOINT 2

Microstep | Current | Voltage | Limit switch DIR | ENABLE
1600 | PK 2.7A | 36V | HIGH | LOW

Wires for my setup: red,yellow,orange,purple (B-,B+,A-,A+)
Control pins: PULS+,GND,DIR+,GND,ENA+

JOINT 1

Microstep | Current | Voltage | Limit switch DIR | ENABLE
1600 | PK 2.7A | 24V | HIGH | LOW

Wires for my setup: red,blue,black,green (A+,A-,B+,B-)
Control pins: GND,ENA+,GND,DIR+,GND,PULS+

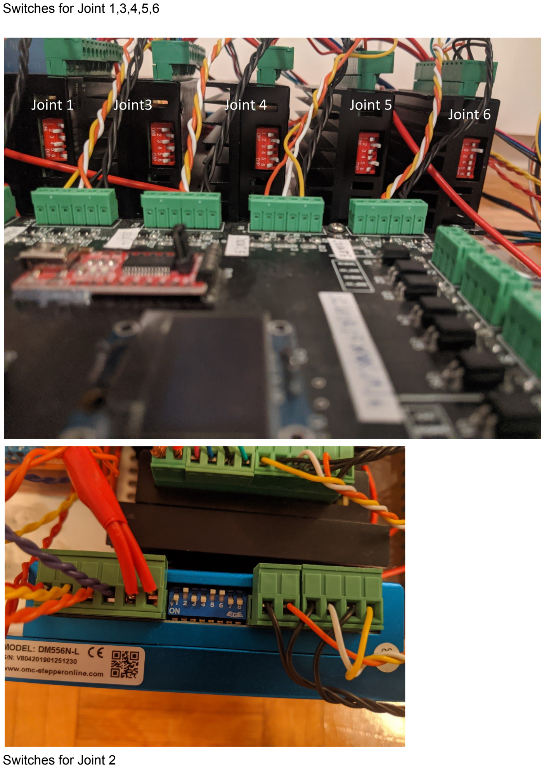
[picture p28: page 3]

Switches for Joint 1,3,4,5,6

Switches for Joint 2

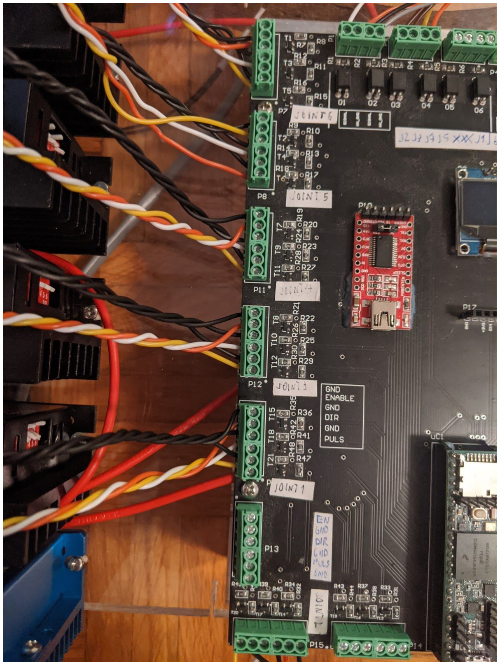
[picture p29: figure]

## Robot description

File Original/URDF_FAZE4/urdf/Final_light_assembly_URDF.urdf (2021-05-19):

<robot name="Final_light_assembly_URDF">
  <link name="base_link">
    <inertial>
      <origin xyz="0.0754452420016786 0.0706653851885525 0.174716050606158" rpy="0 0 0" />
      <mass value="1.75590983031249" />
      <inertia ixx="0.0106901651591523" ixy="1.2533292416581E-05" ixz="-1.78802486116636E-05" iyy="0.0121389538778755" iyz="-0.0001726147454493" izz="0.00523087609446992" />
    </inertial>
    <visual>
      <origin xyz="0 0 0" rpy="0 0 0" />
      <geometry>
        <mesh filename="package://Final_light_assembly_URDF/meshes/base_link.STL" />
      </geometry>
      <material name="">
        <color rgba="0.792156862745098 0.819607843137255 0.933333333333333 1" />
      </material>
    </visual>
    <collision>
      <origin xyz="0 0 0" rpy="0 0 0" />
      <geometry>
        <mesh filename="package://Final_light_assembly_URDF/meshes/base_link.STL" />
      </geometry>
    </collision>
  </link>
  <link name="rotary_base">
    <inertial>
      <origin xyz="3.6594E-07 -0.12491 -0.0091222" rpy="0 0 0" />
      <mass value="1.8968" />
      <inertia ixx="0.011703" ixy="6.2683E-07" ixz="2.7765E-07" iyy="0.010005" iyz="-0.00096832" izz="0.0065158" />
    </inertial>
    <visual>
      <origin xyz="0 0 0" rpy="0 0 0" />
      <geometry>
        <mesh filename="package://Final_light_assembly_URDF/meshes/rotary_base.STL" />
      </geometry>
      <material name="">
        <color rgba="0.79216 0.81961 0.93333 1" />
      </material>
    </visual>
    <collision>
      <origin xyz="0 0 0" rpy="0 0 0" />
      <geometry>
        <mesh filename="package://Final_light_assembly_URDF/meshes/rotary_base.STL" />
      </geometry>
    </collision>
  </link>
  <joint name="rotary_base" type="continuous">
    <origin xyz="0.075629 -0.21266 0.050734" rpy="-1.5708 -6.123E-17 -1.5708" />
    <parent link="base_link" />
    <child link="rotary_base" />
    <axis xyz="0 -1 0" />
  </joint>
  <link name="nadlaktica">
    <inertial>
      <origin xyz="0.11187 -0.011704 0.007695" rpy="0 0 0" />
      <mass value="3.097" />
      <inertia ixx="0.011686" ixy="0.0012432" ixz="-0.0018781" iyy="0.03891" iyz="-5.4012E-05" izz="0.032612" />
    </inertial>
    <visual>
      <origin xyz="0 0 0" rpy="0 0 0" />
      <geometry>
        <mesh filename="package://Final_light_assembly_URDF/meshes/nadlaktica.STL" />
      </geometry>
      <material name="">
        <color rgba="0.79216 0.81961 0.93333 1" />
      </material>
    </visual>
    <collision>
      <origin xyz="0 0 0" rpy="0 0 0" />
      <geometry>
        <mesh filename="package://Final_light_assembly_URDF/meshes/nadlaktica.STL" />
      </geometry>
    </collision>
  </link>
  <joint name="nadlaktica" type="continuous">
    <origin xyz="0 -0.20182 0" rpy="2.7756E-15 -1.3878E-15 -1.8111" />
    <parent link="rotary_base" />
    <child link="nadlaktica" />
    <axis xyz="0 0 1" />
  </joint>
  <link name="lakat">
    <inertial>
      <origin xyz="0.020310022580536 -0.0354589471585284 0.00171229454365077" rpy="0 0 0" />
      <mass value="1.2726491805247" />
      <inertia ixx="0.00430935066273582" ixy="-0.000472663673983171" ixz="2.10793692092687E-05" iyy="0.00388873322685888" iyz="-0.000102922808916268" izz="0.00512549454697952" />
    </inertial>
    <visual>
      <origin xyz="0 0 0" rpy="0 0 0" />
      <geometry>
        <mesh filename="package://Final_light_assembly_URDF/meshes/lakat.STL" />
      </geometry>
      <material name="">
        <color rgba="0.792156862745098 0.819607843137255 0.933333333333333 1" />
      </material>
    </visual>
    <collision>
      <origin xyz="0 0 0" rpy="0 0 0" />
      <geometry>
        <mesh filename="package://Final_light_assembly_URDF/meshes/lakat.STL" />
      </geometry>
    </collision>
  </link>
  <joint name="lakat" type="continuous">
    <origin xyz="0.32 0 0" rpy="3.1416 -6.3895E-16 -1.1753" />
    <parent link="nadlaktica" />
    <child link="lakat" />
    <axis xyz="0 0 -1" />
  </joint>
  <link name="podlaktica">
    <inertial>
      <origin xyz="0.015666 0.10444 0.04524" rpy="0 0 0" />
      <mass value="0.8658" />
      <inertia ixx="0.0043737" ixy="-0.00033248" ixz="-0.00029637" iyy="0.0017275" iyz="-0.0011009" izz="0.0039233" />
    </inertial>
    <visual>
      <origin xyz="0 0 0" rpy="0 0 0" />
      <geometry>
        <mesh filename="package://Final_light_assembly_URDF/meshes/podlaktica.STL" />
      </geometry>
      <material name="">
        <color rgba="0.79216 0.81961 0.93333 1" />
      </material>
    </visual>
    <collision>
      <origin xyz="0 0 0" rpy="0 0 0" />
      <geometry>
        <mesh filename="package://Final_light_assembly_URDF/meshes/podlaktica.STL" />
      </geometry>
    </collision>
  </link>
  <joint name="podlaktica" type="continuous">
    <origin xyz="0 -0.0735 0" rpy="-0.5648 -0.78173 1.7809" />
    <parent link="lakat" />
    <child link="podlaktica" />
    <axis xyz="0.14804 0.90477 0.39934" />
  </joint>
  <link name="saka">
    <inertial>
      <origin xyz="0.00102127447654127 0.00173769308862193 -0.00307332521672926" rpy="0 0 0" />
      <mass value="0.195660541483626" />
      <inertia ixx="0.000196163267087824" ixy="-1.19915207726741E-07" ixz="-4.99910323817217E-07" iyy="0.000195263940589931" iyz="9.07364788265256E-06" izz="0.000136132402412911" />
    </inertial>
    <visual>
      <origin xyz="0 0 0" rpy="0 0 0" />
      <geometry>
        <mesh filename="package://Final_light_assembly_URDF/meshes/saka.STL" />
      </geometry>
      <material name="">
        <color rgba="0.792156862745098 0.819607843137255 0.933333333333333 1" />
      </material>
    </visual>
    <collision>
      <origin xyz="0 0 0" rpy="0 0 0" />
      <geometry>
        <mesh filename="package://Final_light_assembly_URDF/meshes/saka.STL" />
      </geometry>
    </collision>
  </link>
  <joint name="saka" type="continuous">
    <origin xyz="0.037114 0.22683 0.10011" rpy="2.2965 -0.74045 -0.57161" />
    <parent link="podlaktica" />
    <child link="saka" />
    <axis xyz="-1 0 0" />
  </joint>
  <link name="hvataljka">
    <inertial>
      <origin xyz="0.00017222 0.00017758 0.00947" rpy="0 0 0" />
      <mass value="0.020284" />
      <inertia ixx="3.4622E-06" ixy="-9.927E-08" ixz="-2.2616E-08" iyy="3.4561E-06" iyz="-2.332E-08" izz="6.3508E-06" />
    </inertial>
    <visual>
      <origin xyz="0 0 0" rpy="0 0 0" />
      <geometry>
        <mesh filename="package://Final_light_assembly_URDF/meshes/hvataljka.STL" />
      </geometry>
      <material name="">
        <color rgba="0.79216 0.81961 0.93333 1" />
      </material>
    </visual>
    <collision>
      <origin xyz="0 0 0" rpy="0 0 0" />
      <geometry>
        <mesh filename="package://Final_light_assembly_URDF/meshes/hvataljka.STL" />
      </geometry>
    </collision>
  </link>
  <joint name="hvataljka" type="continuous">
    <origin xyz="0 0 -0.042312" rpy="-3.1416 2.5362E-15 0.2419" />
    <parent link="saka" />
    <child link="hvataljka" />
    <axis xyz="0 0 1" />
  </joint>
</robot>

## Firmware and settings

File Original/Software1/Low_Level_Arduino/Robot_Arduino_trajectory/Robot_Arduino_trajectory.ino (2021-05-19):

/*************************************************************************
  By: Petar Crnjak
  version: 2.0
  For more info visit:
  https://github.com/PCrnjak/Faze4-Robotic-arm
**************************************************************************/

#include <Arduino.h>

/*****************************************************************************
  Define pins on pcb
  Defined by the name near the connector.
******************************************************************************/
#define pi 3.1415926535
// Joint6
// Port on PCB board P7
#define enable6 35    // port1  
#define dir6    36    // port2  
#define puls6   37    // port3  

// Joint5
//Port on PCB board P8 // On this connector pins for enable and puls are switched
// so our puls pin on board is connected to enable pin and our enable pin is connected to pulse pin
#define enable5 A21   // port6    
#define dir5    39    // port5  
#define puls5   38    // port4  

// Joint4
//
#define enable4 A22   // port7   analogWrite(A21, (int)val); rezolucija 12
#define dir4    13    // port8 // LED_BUILTIN  
#define puls4   14    // port9  

// Joint3
//Port on PCB board P12
#define enable3 15    // port10  
#define dir3    16    // port11  
#define puls3   17    // port12  

// Joint1
//Port on PCB board P16
#define enable1 20    // port13  
#define dir1    21    // port14  
#define puls1   22    // port15  

// Extra 1
//Port on PCB board P13
#define enable_ex1 2     // port16  
#define dir_ex1    1     // port17  
#define puls_ex1   0    // port18  

//Joint 2
//Port on PCB board P15
#define enable2 5     // port21  
#define dir2    4     // port20  
#define puls2   3     // port19  

// Extra 2
//Port on PCB board P14
#define enable_ex2 8     // port24  
#define dir_ex2    7     // port23  
#define puls_ex2   6     // port22  

//Port on PCB board P20
#define Gripper 23

//Inputs from left to right
#define limit2 28        // O1  
#define limit3 27        // O2  
#define limit4 26        // O3  
#define limit5 25        // O4  
#define limit_ex1 24     // O5  
#define limit_ex2 12     // O6  
#define limit_ex3 9      // O7   
#define limit1 10        // O8  
#define limit6 11        // O9   

// EXTRA PINS from top to bottom
// first is GND
#define ex1 29
#define ex2 30

int angle1[1000] = {};
int angle2[1000] = {};
int angle3[1000] = {};
int angle4[1000] = {};
int angle5[1000] = {};
int angle6[1000] = {};

int speed1[1000] = {};
int speed2[1000] = {};
int speed3[1000] = {};
int speed4[1000] = {};
int speed5[1000] = {};
int speed6[1000] = {};

const int EnablePin[] = {enable1, enable2, enable3, enable4, enable5, enable6}; // pins that enable stepper drivers

const int stepPin[] = {puls1, puls2, puls3, puls4, puls5, puls6}; // STEP pins on stepper drivers, first in array is joint 1, last i joint 6

const int dirPin[] = {dir1, dir2, dir3, dir4, dir5, dir6}; // DIR pins on stepper driver, first in array is joint 1 ,last is joint 6

const int LimitPin[] = {limit1, limit2, limit3, limit4, limit5, limit6}; // Pins for limit switches and inductive sensors

const int joint[7] = {0, 0, 1, 2, 3, 4, 5}; //// Calls---> Joint[1]=0 , Joint[2]=1...

const int meh_limit[] = {20000, 24000, 7000, 4000, 2600, 7700}; //Mechanical limits of joints.Represented in number of steps

const float gear_ratio[] = {25 , 27 , 15 , 11.847 , 11 , 19.19};

const float step_angle[] = {1.8 , 1.8 , 0.9 , 1.8 , 1.8 , 1.8};

const float microstep[] = {0.125 , 0.125 , 0.25 , 0.5 , 0.5 , 0.5};

bool zeroed[] = {0, 0, 0, 0, 0, 0}; // state variables that tell us if joint is zeroed or not

bool state[] = {0, 0, 0, 0, 0, 0}; // used in move_routine functions TODO test statis

unsigned long previousMillis[] = {0, 0, 0, 0, 0, 0};

int current_pulse_widht[] = {1000, 800, 1200, 900, 900, 900}; // current speed we are moving at

signed int current_position[] = {0, 0, 0, 0, 0, 0}; // our current position , never change this value manually after homing routine
signed int needed_position[] = {0, 0, 0, 0, 0, 0}; // position we want to go to

unsigned long currentMillis = 0;

volatile int error = 0; // Top level condition for robot to work , if 1 robot locks

uint16_t vars2[] = {0,0,0,0,0,0,0,0,0,0,0,0};

int m = 0;
int m_ = 0;
bool flag4 = 0;
bool flag5 = 0;

/*****************************************************************************
  Extra UART ports
 ******************************************************************************/
// RX5 = 34
// TX5 = 33
// RX4 = 31
// TX4 = 32

/*****************************************************************************
   OLED PINS
 ******************************************************************************/
// SDA = 18
// SCL = 19

/*****************************************************************************
    Prototype for used functions
 ******************************************************************************/
void Homing_routine(int joint_num);
void homeAll();
void move_all();
void move_routine_backward(int joint_num);
void move_routine_forward(int joint_num);
void false_swtich_trigger_function1(void);
void false_swtich_trigger_function2(void);
void false_swtich_trigger_function3(void);
void false_swtich_trigger_function4(void);
void false_swtich_trigger_function5(void);
void false_swtich_trigger_function6(void);
void get_data();
void robot_setup();
void get_data_2();
void data_test();
void first_pos();
void trajectory();

void setup() {

  Serial.begin(9600);
  while(!Serial){};
  Serial4.begin(9600);
  delay(1000);
  Serial4.println("Robot is starting , please wait");
  Serial4.println("...");
  Serial4.print("\n");

  delay(100);

  pinMode(LimitPin[joint[1]], INPUT_PULLUP);
  pinMode(EnablePin[joint[1]], OUTPUT);
  pinMode(stepPin[joint[1]], OUTPUT);
  pinMode(dirPin[joint[1]], OUTPUT);
  digitalWrite(dirPin[joint[1]], HIGH);

  pinMode(LimitPin[joint[2]], INPUT_PULLDOWN);
  pinMode(EnablePin[joint[2]], OUTPUT);
  pinMode(stepPin[joint[2]], OUTPUT);
  pinMode(dirPin[joint[2]], OUTPUT);
  digitalWrite(dirPin[joint[2]], HIGH);

  pinMode(LimitPin[joint[3]], INPUT_PULLDOWN);
  pinMode(EnablePin[joint[3]], OUTPUT);
  pinMode(stepPin[joint[3]], OUTPUT);
  pinMode(dirPin[joint[3]], OUTPUT);
  digitalWrite(dirPin[joint[3]], HIGH);

  pinMode(LimitPin[joint[4]], INPUT_PULLDOWN);
  pinMode(EnablePin[joint[4]], OUTPUT);
  pinMode(stepPin[joint[4]], OUTPUT);
  pinMode(dirPin[joint[4]], OUTPUT);
  digitalWrite(dirPin[joint[4]], HIGH);

  pinMode(LimitPin[joint[5]], INPUT_PULLDOWN);
  pinMode(EnablePin[joint[5]], OUTPUT);
  pinMode(stepPin[joint[5]], OUTPUT);
  pinMode(dirPin[joint[5]], OUTPUT);
  digitalWrite(dirPin[joint[5]], HIGH);

  pinMode(LimitPin[joint[6]], INPUT_PULLUP);
  pinMode(EnablePin[joint[6]], OUTPUT);
  pinMode(stepPin[joint[6]], OUTPUT);
  pinMode(dirPin[joint[6]], OUTPUT);
  digitalWrite(dirPin[joint[6]], HIGH);

  attachInterrupt(limit1, false_swtich_trigger_function1, FALLING);
  attachInterrupt(limit2, false_swtich_trigger_function2, RISING);
  attachInterrupt(limit3, false_swtich_trigger_function3, RISING);
  attachInterrupt(limit4, false_swtich_trigger_function4, RISING);
  attachInterrupt(limit5, false_swtich_trigger_function5, RISING);
  attachInterrupt(limit6, false_swtich_trigger_function6, FALLING);

  delay(5000);

  homeAll();

  detachInterrupt(limit1);
  detachInterrupt(limit2);
  detachInterrupt(limit3);
  detachInterrupt(limit4);
  detachInterrupt(limit5);
  detachInterrupt(limit6);

  current_pulse_widht[joint[1]] = 800;
  current_pulse_widht[joint[2]] = 900;
  current_pulse_widht[joint[3]] = 1200;
  current_pulse_widht[joint[4]] = 900;
  current_pulse_widht[joint[5]] = 900;
  current_pulse_widht[joint[6]] = 900;

 
  //Serial4.begin(9600);
  delay(1000);
  //Serial4.println("Robot is starting , please wait");
  //Serial4.println("...");
  //Serial4.print("\n");


}

void loop() {
  robot_setup();
  //data_test();
  first_pos();
  delay(1000);
  // goto first position
  while (error == 0) {
    //get_data();
    //move_all();
    trajectory();

  }
}


  void homeAll() {

    int flag = 0;
    /*****************************************************************************
      detach interrupts , if we dont do this robot will lock itself up
      ******************************************************************************/
    detachInterrupt(limit1);
    detachInterrupt(limit2);
    detachInterrupt(limit3);
    detachInterrupt(limit4);
    detachInterrupt(limit5);
    detachInterrupt(limit6);
    /*****************************************************************************
      Set speed for homing routines
    ******************************************************************************/
    current_pulse_widht[joint[1]] = 1500;
    current_pulse_widht[joint[2]] = 1500;
    current_pulse_widht[joint[3]] = 1500;
    current_pulse_widht[joint[4]] = 1500;
    current_pulse_widht[joint[5]] = 1500;
    current_pulse_widht[joint[6]] = 1500;
    /*****************************************************************************
        Enable all motors TODO joints that are on DACS
     ******************************************************************************/

    digitalWrite(EnablePin[joint[1]], LOW);
    delay(200);
    digitalWrite(EnablePin[joint[2]], LOW);
    delay(200);
    digitalWrite(EnablePin[joint[3]], LOW);
    delay(200);
    analogWrite(EnablePin[joint[5]], 0);
    delay(200);
    analogWrite(EnablePin[joint[4]], 0);
    delay(200);
    digitalWrite(EnablePin[joint[6]], LOW);

    /*****************************************************************************
         Set direction for all motors
    ******************************************************************************/
    digitalWrite(dirPin[joint[1]], HIGH);
    digitalWrite(dirPin[joint[2]], HIGH);
    digitalWrite(dirPin[joint[3]], HIGH);
    digitalWrite(dirPin[joint[4]], HIGH);
    digitalWrite(dirPin[joint[5]], HIGH);
    digitalWrite(dirPin[joint[6]], LOW);

    /*****************************************************************************
      Home joints 6 ,5 and 4
    ******************************************************************************/
    int i = 0;
    while ((zeroed[joint[6]] != 1)  or (zeroed[joint[5]] != 1) or (zeroed[joint[4]] != 1)) {

      Homing_routine(joint[4]);
      Homing_routine(joint[5]);
      Homing_routine(joint[6]);

      /*****************************************************************************
        Robot lock
      ******************************************************************************/
      //while (flag == 1) {}

      /*****************************************************************************
         check if we are moving to much to home the motor
         if we do lock the robot
         ******************************************************************************/
      for (i = 4; i < 7; i++) {
        if ((current_position[joint[i]] + 50) >= meh_limit[joint[i]]) {
          Serial4.println("Error: It took too long for joint ");
          Serial4.print(i);
          Serial4.print(" s limit switch to trigger, restart your controller");
          flag = 1;
          break;

        }

      }

    }

    /*****************************************************************************
       Set current positions to 0 since we hit our homing switches
    ******************************************************************************/
    current_position[joint[6]] = 75;
    current_position[joint[5]] = 0;
    current_position[joint[4]] = 0;
    delay(500);
    /*****************************************************************************
      Now we will move from those limit switches for specific amounts
       We are doing this so that robot will never hit limit switches in normal operation
      In the same step we also move them to standby position              (this is position in kinematics
        diagram where all joints are in 0 position)
       We dont need to offset joint 6 since it is continous rotation joint
      We offset current position by :
      .  *            Joint 5 = offset 110 = new 0 , standby positon new = 1173
                  Joint 4 = offset 110 = new 0 , standby positon new = 2275
    ******************************************************************************/
    needed_position[joint[6]] = 0;

    needed_position[joint[5]] = 1283;

    needed_position[joint[4]] = 2385;

    while (needed_position[joint[6]] != current_position[joint[6]] or needed_position[joint[5]] != current_position[joint[5]] or needed_position[joint[4]] != current_position[joint[4]] ) {
      move_all();

    }

    /*****************************************************************************
       These positons represent robot in its standby position
       This position would be 0 positions in robot kinematic diagram.
    ******************************************************************************/
    current_position[joint[6]] = 3838;
    needed_position[joint[6]] = 3838;

    current_position[joint[5]] = 1173;
    needed_position[joint[5]] = 1173;

    current_position[joint[4]] = 2275;
    needed_position[joint[4]] = 2275;

    /*****************************************************************************
         Home only joint 3
     ******************************************************************************/
    delay(200);
    while ((zeroed[joint[3]] != 1)) {
      Homing_routine(joint[3]);
      while (flag == 1) {}
      if ((current_position[joint[3]] + 50) >= meh_limit[joint[3]]) {
        Serial4.println("Error: It took too long for joint ");
        Serial4.print(3);
        Serial4.print(" s limit switch to trigger, restart your controller");
        flag = 1;
        break;

      }

    }

    /*****************************************************************************
      Here we only move from limit switch , and will later move with joint 2 to
       standby position
     ******************************************************************************/

    delay(100);
    current_position[joint[3]] = 0;
    needed_position[joint[3]] = 350;

    while (needed_position[joint[3]] != current_position[joint[3]]  ) {
      move_all();

    }
    current_position[joint[3]] = 0;
    needed_position[joint[3]] = 0;

    /*****************************************************************************
      Home only joint 2
    ******************************************************************************/
    delay(200);
    while ((zeroed[joint[2]] != 1)) {
      Homing_routine(joint[2]);
      //while (flag == 1) {}
      if ((current_position[joint[2]] + 50) >= meh_limit[joint[2]]) {
        Serial4.println("Error: It took too long for joint ");
        Serial4.print(2);
        Serial4.print(" s limit switch to trigger, restart your controller");
        flag = 1;
        break;

      }

    }

    /*****************************************************************************
       Here we only move from limit switch , and will later move with joint 3 to
      standby position
    ******************************************************************************/

    delay(100);
    current_position[joint[2]] = 0;
    needed_position[joint[2]] = 700;

    while (needed_position[joint[2]] != current_position[joint[2]] ) {
      move_all();

    }

    current_position[joint[2]] = 0;
    needed_position[joint[2]] = 0;

    /*****************************************************************************
      Home only joint 1
    ******************************************************************************/

    delay(200);
    while ((zeroed[joint[1]] != 1)) {
      //while (flag == 1) {}
      Homing_routine(joint[1]);
      if ((current_position[joint[1]] + 50) >= meh_limit[joint[1]]) {
        Serial4.println("Error: It took too long for joint ");
        Serial4.print(1);
        Serial4.print(" s limit switch to trigger, restart your controller");
        flag = 1;
        break;

      }

    }

    delay(100);
    current_position[joint[1]] = 10000;
    needed_position[joint[1]] = 9500; //10500
    delay(5);

    while (needed_position[joint[1]] != current_position[joint[1]]  ) {
      move_all();

    }

    current_position[joint[1]] = 10000;
    needed_position[joint[1]] = 10000;

    /*****************************************************************************
       Move joints 2 and 3 to standby positons
      .  ******************************************************************************/
    digitalWrite(dirPin[joint[2]], LOW);
    needed_position[joint[2]] = 10000 ;

    digitalWrite(dirPin[joint[3]], LOW);
    needed_position[joint[3]] = 2650;

    while (needed_position[joint[2]] != current_position[joint[2]] or needed_position[joint[3]] != current_position[joint[3]]) {
      move_all();

    }

    /*****************************************************************************
      Attach interrupts
      They should never activate in normal operation
      We do not attach interrupts for limit 1 and 6
    ******************************************************************************/

    //attachInterrupt(limit1, false_swtich_trigger_function1, FALLING);
    attachInterrupt(limit2, false_swtich_trigger_function2, RISING);
    attachInterrupt(limit3, false_swtich_trigger_function3, RISING);
    attachInterrupt(limit4, false_swtich_trigger_function4, RISING);
    attachInterrupt(limit5, false_swtich_trigger_function5, RISING);
    //attachInterrupt(limit6, false_swtich_trigger_function6, FALLING);

  }

  /*****************************************************************************
    Similar to move forward/backward but has extra steps
      to check if switches are pressed
  ******************************************************************************/
  void Homing_routine(int joint_num) {
    if (digitalRead(LimitPin[joint_num]) == LOW) {
      currentMillis = micros();
      //// state is used to prevent triggering of this if statement twice in row
      ///// same goes for second one , this secures perfect square wave form
      if (currentMillis - previousMillis[joint_num] >= current_pulse_widht[joint_num] and state[joint_num] == 0) {
        previousMillis[joint_num] = currentMillis;
        digitalWrite(stepPin[joint_num], HIGH);
        state[joint_num] = 1;

      }
      else if (currentMillis - previousMillis[joint_num] >= current_pulse_widht[joint_num] and state[joint_num] == 1) {
        previousMillis[joint_num] = currentMillis;
        digitalWrite(stepPin[joint_num], LOW);
        state[joint_num] = 0;
        current_position[joint_num] = current_position[joint_num] + 1;


      }

    }
    if (digitalRead(LimitPin[joint_num]) == HIGH and zeroed[joint_num] == 0 ) {
      current_position[joint_num] = 0;
      Serial4.println("Joint ");
      Serial4.print(joint_num + 1);
      Serial4.println(" in 0 position.");
      zeroed[joint_num] = 1;

    }

  }

  /*****************************************************************************
    Function that checks if we are at desired position
      If we are not move until we are
   ******************************************************************************/
  void move_all() {

    if (needed_position[joint[1]] > current_position[joint[1]] ) {
      digitalWrite(dirPin[joint[1]], LOW);
      move_routine_forward(joint[1]);

    }
    else if (needed_position[joint[1]] < current_position[joint[1]] ) {
      digitalWrite(dirPin[joint[1]], HIGH);
      move_routine_backward(joint[1]);

    }
    if (needed_position[joint[2]] > current_position[joint[2]] ) {
      digitalWrite(dirPin[joint[2]], LOW);
      move_routine_forward(joint[2]);

    }
    else if (needed_position[joint[2]] < current_position[joint[2]] ) {
      digitalWrite(dirPin[joint[2]], HIGH);
      move_routine_backward(joint[2]);

    }
    if (needed_position[joint[3]] > current_position[joint[3]]) {
      digitalWrite(dirPin[joint[3]], LOW);
      move_routine_forward(joint[3]);

    }
    else if (needed_position[joint[3]] < current_position[joint[3]] ) {
      digitalWrite(dirPin[joint[3]], HIGH);
      move_routine_backward(joint[3]);

    }
    if (needed_position[joint[4]] > current_position[joint[4]] ) {
      digitalWrite(dirPin[joint[4]], LOW);
      move_routine_forward(joint[4]);

    }
    else if (needed_position[joint[4]] < current_position[joint[4]] ) {
      digitalWrite(dirPin[joint[4]], HIGH);
      move_routine_backward(joint[4]);

    }
    if (needed_position[joint[5]] > current_position[joint[5]] ) {
      digitalWrite(dirPin[joint[5]], LOW);
      move_routine_forward(joint[5]);

    }
    else if (needed_position[joint[5]] < current_position[joint[5]]) {
      digitalWrite(dirPin[joint[5]], HIGH);
      move_routine_backward(joint[5]);

    }
    if (needed_position[joint[6]] > current_position[joint[6]] ) {
      digitalWrite(dirPin[joint[6]], HIGH);
      move_routine_forward(joint[6]);

    }
    else if (needed_position[joint[6]] < current_position[joint[6]] ) {
      digitalWrite(dirPin[joint[6]], LOW);
      move_routine_backward(joint[6]);

    }

  }

  /*****************************************************************************
      Routine to move forward
   ******************************************************************************/
  void move_routine_forward(int joint_num) {
    currentMillis = micros();
    ///state is used to prevent triggering of this if statement twice in row
    // same goes for second one , this secures perfect square wave form
    if (currentMillis - previousMillis[joint_num] >= current_pulse_widht[joint_num] and state[joint_num] == 0) {
      previousMillis[joint_num] = currentMillis;
      digitalWrite(stepPin[joint_num], HIGH);
      state[joint_num] = 1;

    }
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

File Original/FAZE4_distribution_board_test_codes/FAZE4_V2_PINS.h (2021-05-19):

#define LIMIT1 11
#define LIMIT2 10
#define LIMIT3 9
#define LIMIT4 8
#define LIMIT5 7
#define LIMIT6 6
#define SENSOR1 5
#define SENSOR2 2
#define SENSOR3 1


#define PUL1 12
#define DIR1 24
#define ENA1 25

#define PUL2 26
#define DIR2 27
#define ENA2 28

#define PUL3 29
#define DIR3 30
#define ENA3 35

#define PUL4 36
#define DIR4 37
#define ENA4 38

#define PUL5 39
#define DIR5 13
#define ENA5 14

#define PUL6 15
#define DIR6 16
#define ENA6 17

#define PUL7 18
#define DIR7 19
#define ENA7 20

#define PUL8 21
#define DIR8 22
#define ENA8 23

#define GRIPPER 0

#define SDA_2 43
#define SCL_2 44

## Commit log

2021-05-19 added STL folder
2021-05-19 extracted stl and updated links to be local
    [11_1 cyclo disc.STL, 15_1 cyclo disc.STL, 26 teeth Joint 4 pulley.STL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]
2021-05-19 added bom and listed 3D prints
2021-05-19 linked wrist STL files
    [Joint-6-output-shaft.stl, Wrist-case.stl, Wrist-cover.stl]
2021-05-19 added 3D prints for Wrist
    [Joint-6-output-shaft.3mf, Wrist-case.3mf, Wrist-cover.3mf]
2021-05-20 added consolidated bom.md with the screws ordered
2021-05-20 renamed wrist folder
    [Joint-6-output-shaft.3mf, Joint-6-output-shaft.stl, Wrist-case.3mf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]
2021-05-20 fixed links in wrist, added forearm BoM + STL list
2021-05-24 added quantity to 3d prints
2021-05-24 consistent renaming of stl files
    [11_1 cyclo disc.STL, Forearm main case.STL, Forearm top cover.STL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]
2021-05-24 Added 3D print files and links to them
    [11_1 cyclo disc.3mf, Forearm main case.3mf, Forearm top cover.3mf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]
2021-05-25 added ball bearings to overall bom
2021-05-29 extended bom file to include all from the excel
2021-06-07 started c_Ellbow
    added gcode and 3mf
    replaced gcode by rar due to file size
    [11_1 cyclo disc.STL, 15_1 cyclo disc.STL, 26 teeth Joint 4 pulley.STL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]
2021-06-21 updated joint 6 and created first test
    [Joint-6-output-shaft-5mm-brass-insert.stl, Joint-6-output-shaft.3mf]

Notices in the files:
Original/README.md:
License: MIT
